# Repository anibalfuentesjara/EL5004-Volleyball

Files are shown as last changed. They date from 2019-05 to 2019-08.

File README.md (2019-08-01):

# EL5004-Volleyball
EL5004 Taller de diseño - Beauchef Proyecta. Proyecto de lanzador de balones de volleyball.

El objetivo del proyecto es realizar un lanzador de balones de volleyball, con el fin de facilitar los entrenamientos del DR de volleyball de la Universidad de Chile y de la rama de volleyball de la universidad. Para esto se trabaja en conjunto con equipos de Ingeniería Eléctrica e Ingeniería Mecánica. El sistema tiene como requisito el poder apuntar el lanzador, ajustar la velocidad de lanzamiento e incorporar un sistema de detección de personas y distintas rutinas de práctica.

El repositorio cuenta con lo siguiente:

- Informe: informe final del ramo.

- Presentación: presentación final del ramo.

- Omni Wrist III: Diseños stl, Solid Edge y Fusion 360 para la base del sistema. Esta base consiste en el sistema Omni Wrist III, que a través de dos motores logra apuntar en los ejes de libertad Pitch y Roll.

- Códigos motor: códigos en arduino para el movimiento de los motores.

- Person Volley: sistema de visión computacional desarrollado en python mediante la librería pytorch. Es el mismo que se adjunta en el github de visión.

- Parabolas: cálculo de parábolas en el lanzamiento del balón.

- Planos eléctricos y lista de materiales: lista de materiales y hardware eléctrico.

- demo: código de arduino que recibe señales de control desde python y mueve servomotores. Es usado en la demo con el modelo 3D impreso.

- comunicacion_wifi: códigos para comunicación wifi entre python y arduino.

- fin de carrera: códigos de fines de carrera.

## Google Drive

Se presentan diversos videos grabados en prácticas del DR.

https://drive.google.com/drive/folders/1kx5sKdnLs_XCrbL7N90hBN0Ewg4CD0pJ

## Sistema de vision

Se presenta el github del sistema de visión y el google drive con los pesos utilizados por el sistema de visión.

https://github.com/Jackerz312/Person_Volley

https://drive.google.com/drive/folders/1hPUGl7ACIlWxsmZmfyyrUkmBOFc591Y6?usp=sharing

## Demo

Se realiza una remo con el modelo del omniwrist impreso en 3D. Para correr la demo el esquemático del circuito es el siguiente:

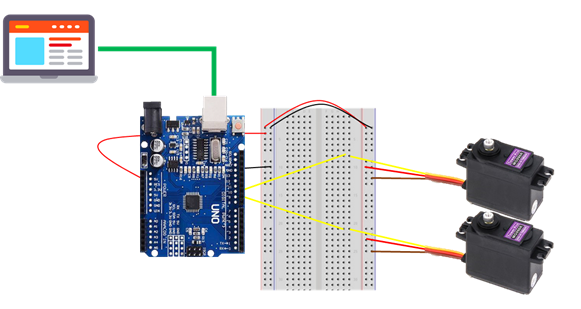
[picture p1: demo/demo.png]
Esquematico demo


Se debe tener cuidado de conectar cada servo en el pin correspondiente. El arduino debe estar conectado con el computador mediante usb. Se debe cargar en arduino el programa demo.ino de la carpeta demo, teniendo cuidado de tener conectado el servo 1 al pin 9 y el servo 2 al pin 10. Luego, existen dos programas de python, en la carpeta person_volley:

- demo_seleccion_libre.py: permite seleccionar un punto en la cancha y apuntar el omni-wrist en esa dirección. En la línea 22 del código se debe tener cuidado de seleccionar el puerto donde está conectado el arduino.

- main_tracking.py: permite seleccionar una persona en el sistema de visión computacional y realizar un tracking de la persona. La persona se selecciona haciendo click sobre la persona en el video. En la línea 64 del código se debe tener cuidado de seleccionar el puerto donde está conectado el arduino. Se puede usar un modelo más rápido cambiando en la línea 61 del código por tini=True.

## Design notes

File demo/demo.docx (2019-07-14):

Arduino_python.ino

Descripción general:

El código permite la recepción de datos desde el puerto serial 9600. Esto se utiliza para recibir los datos de movimiento desde Python para luego realizar el movimiento de motores servo.

Lenguaje: Arduino.

Componentes utilizados:

- 1 Arduino Uno.
- 2 motores servo.
- Fuente de poder para Arduino (se utiliza una de 12 volts).
- Omniwrist.

Conexiones (Esquemático):

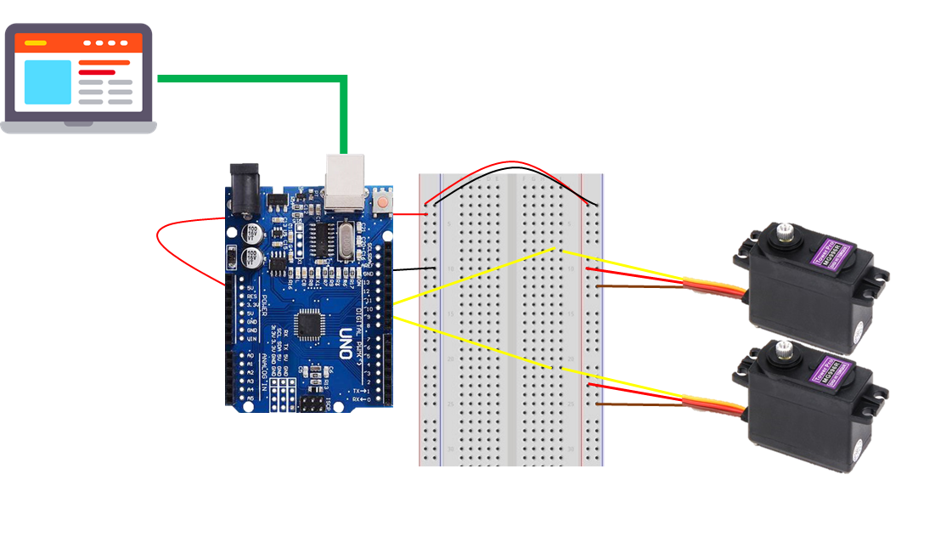
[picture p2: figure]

- Puerto serial en el código debe ser el mismo al que se fije el programa en Python.
- Servos se encuentran conectados al Omniwrist.
- Motores se encuentran conectados a los puertos 9 y 10 en el Arduino.

Descripción del código:

Se inicializan los valores de posición con datos de calibración que permitan que el Omniwrist se ubique en posición vertical.

Se ingresa al loop, que permite la recepción de datos a través del puerto serial. Como lo datos se envían como un String de forma “AnguloServo1#AnguloServo2#VelocidadLanzamiento” se debe pasar los datos a un arreglo de tipo float, para lo que se utiliza la función obtenerDatos.

Posteriormente se les indica esta posición a los motores servo.

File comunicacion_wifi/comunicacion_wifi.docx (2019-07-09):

Comunicación Wifi

La comunicación wifi está encargada de comunicar el computador que procese la parte de visión computacional con el Arduino encargado de mover el lanzador. En particular a través de la comunicación wifi se conecta el computador que procesa el sistema de visión computacional con el Arduino, el cual debe estar conectado al módulo wifi ESP8266 (datasheet https://www.espressif.com/sites/default/files/documentation/0a-esp8266ex_datasheet_en.pdf). Tanto el computador como el Arduino deben estar conectados a la misma red wifi. Los datos a enviar desde el computador al Arduino corresponden a la velocidad de lanzamiento del balón, la elevación de lanzamiento y el ángulo del jugador respecto al lanzador.

En la figura 1 se presenta un esquemático de la conexión del Arduino con el módulo ESP8266.

Figura 1: esquemático de la conexión del Arduino con el módulo wifi ESP8266.

Dentro de los archivos incorporados se encuentra el código SendMessage.py que se ejecuta en Python y envía mediante socket un string al Arduino, el cual será ingresado en la consola donde se ejecute el código Python.

Además, dentro del código está el archivo parsearString.ino que corresponde a un código de Arduino que ejemplifica como parsear datos recibidos como string, los cuales contienen los tres números enviados separados por #, y los guarda como floats en un array; por ejemplo, el código recibe el string 1.32#23.5#44.5 y guarda en el array datos los floats [1.32, 23.5, 44.5]. Se recalca que este código solo ejemplifica el parsear los datos y no utiliza la comunicación wifi.

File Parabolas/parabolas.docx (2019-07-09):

Se presenta el script de Matlab parabolas.m. En este script se simula la trayectoria seguida en un lanzamiento del balón y se proyecta en 2 dimensiones el problema de lanzar el balón de un punto a otro.

El problema se aborda de la siguiente manera:

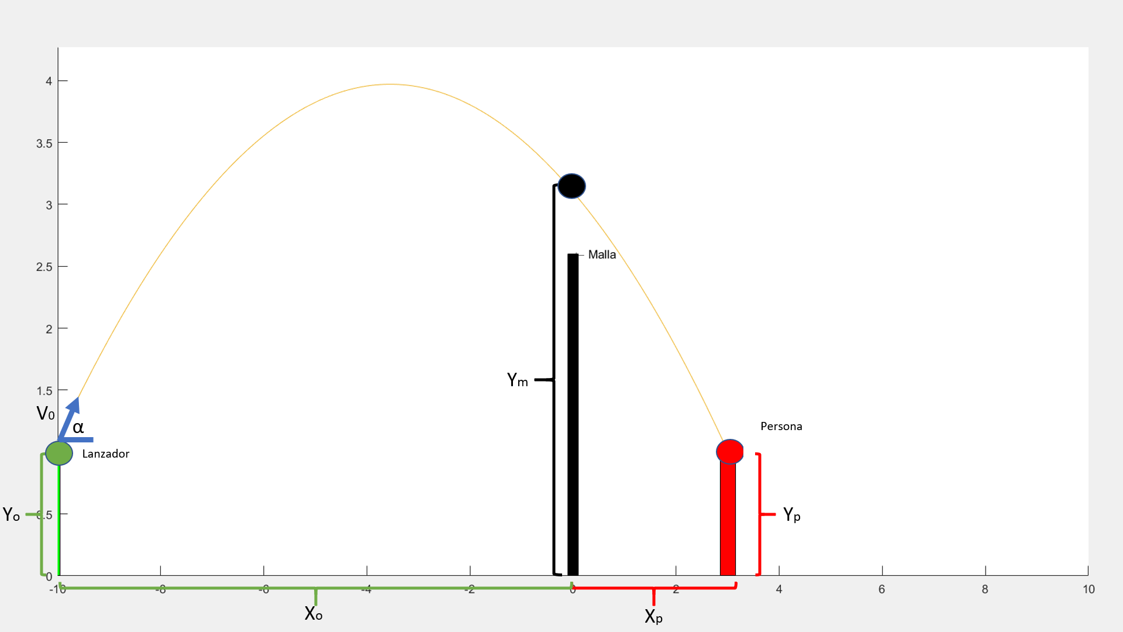
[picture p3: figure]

Dado los puntos (Xo,Yo) representando las coordenadas del lanzador, el punto (0,Ym) representando las coordenadas por la que pasará el balón sobre la malla y las coordenadas (Xp,Yp) representando el punto de recepción del balón; encontrar la velocidad inicial V0 y el ángulo α de elevación con el cual se debe lanzar el balón para que pase por los puntos dados.

Para abordar este problema el primer paso es encontrar la parábola que describe la trayectoria dada; para esto, con los tres puntos disponibles se ajusta una parábola mediante polyfit. Esta parábola está descrita de la forma:

f(x) = A x^2 +Bx+C

Con la ecuación de la parábola posteriormente se encuentra el ángulo de inclinación a través de la pendiente de la parábola evaluada en x = Xo, esto es:

m_(inclinación) =f '(X_o ) = AX_o +B

α=atan(m_(inclinación) )

Una vez encontrado el ángulo se procede a encontrar la velocidad inicial de lanzamiento. Para ello se resuelven las ecuaciones de movimiento del balón considerando los puntos del lanzador y de la persona y descomponiendo la velocidad inicial como:

V_0 =V_0 cos(α)x+V_0 sin(α)y

Las ecuaciones de movimiento se pueden expresar como:

X_p =X_O +V_0 cos(α)T

Y_p =Y_O +V_0 sin(α)T - g T^2

Donde las incógnitas son la velocidad inicial V0 y el tiempo entre el lanzador y la persona igual a T.

Resolviendo este sistema de ecuaciones se llega a:

V_0 =√((0.5g(X_p -X_O )^2)/(cos(α)^2 ((Y_p -Y_O )-tan(α)(X_p -X_O ))))

Y con esto se obtiene el ángulo de inclinación y la velocidad inicial de lanzamiento. Esto es utilizado como base en la parte de visión computacional para calcular los parámetros de lanzamiento del balón.

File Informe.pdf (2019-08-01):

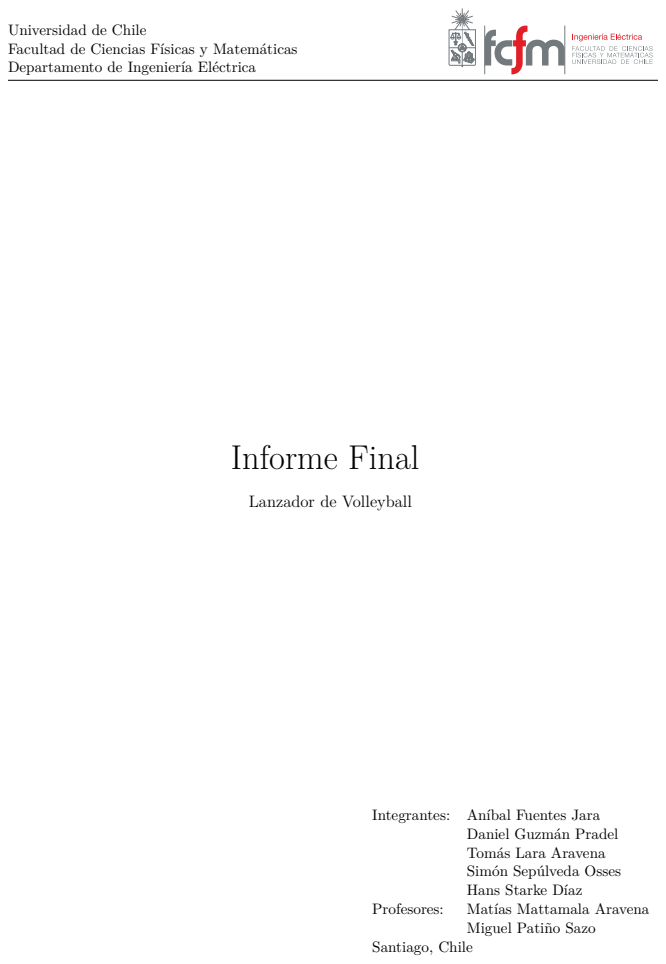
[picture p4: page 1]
Informe Final; Integrantes:; Aníbal Fuentes Jara; Profesores:; Matías Mattamala Aravena; Santiago, Chile

Universidad de Chile
Facultad de Ciencias Físicas y Matemáticas
Departamento de Ingeniería Eléctrica

Lanzador de Volleyball

Daniel Guzmán Pradel
Tomás Lara Aravena
Simón Sepúlveda Osses
Hans Starke Díaz

Miguel Patiño Sazo

Índice de Contenidos | i

# Índice de Contenidos

1. Introducción | 2
2. Solución propuesta | 4
3. Metodología de trabajo | 6
3.1. Equipo de Visión | | 6
| 3.1.1. Detección | | 7
| 3.1.2. Tracking | | 7
| 3.1.3. Transformación de homografía | | 8
3.2. Equipo de Omni-Wrist y Motores | | 8
| 3.2.1. Construcción de Omniwrist | | 9
| 3.2.2. Movimiento con Motores Stepper | | 9
3.2.3. Trabajo con fines de carrera | 10
3.2.4. Cálculo de trayectorias | 11
3.2.5. Ángulos de Giro de motores | 13
3.3. Equipo de Comunicación | 14
3.3.1. ESP8266 | 14
3.3.2. Comunicación con Python | 15
3.3.3. Control de motores | 15
3.3.4. Comunicación Serial | 16
4. Conclusiones y trabajo propuesto | 17

# Lista de Figuras

1 | Esquema de la solución propuesta | | 4
2 | Mecanismo de lanzador | | 5
3 | Esquema sistema de visión computacional | | 6
4 | Diagrama del software de visión computacional | | 7
5 | Puntos seleccionados para realizar la transformación de homografía | | 8
6 | Modelo de omni-wrist III diseñado en fusion 360 e impreso en 3D | | 9
7 | Esquemático de conexión de motores Stepper | 10
8 | Esquemático de conexión de motores Stepper con fines de carrera | 11
9 | Esquema para cálculo de orientación | 12
10 | Esquema para cálculo de elevación y velocidad | 12
11 | Relación entre el ángulo de un motor respecto al reposo, y el ángulo del lanzador. . 13
12 | Módulo ESP8266 | 15
13 | Conexión entre módulo ESP8266 y Arduino | 15
Informe Final | EL5004-3 Taller de Diseño

1

Resumen

En el presente informe se detalla el trabajo realizado durante el curso de taller de diseño Beauchef Proyecta, en el cual se trabajó en el proyecto de lanzador de balones de volleyball.

El proyecto abordado se dividió en tres equipos durante el presente semestre, dos equipos de Ingeniería Mecánica, uno dedicado a la base del lanzador de balones (equipo de omni-wrist) y otro dedicado al lanzador en si (equipo lanzador); el tercer equipo corresponde al equipo eléctrico, cuyo trabajo se detalla en este informe. El trabajo realizado en este equipo esta orientado a la integración del sistema como un todo, centrándose principalmente en tres áreas: el equipo de visión computacional, orientado a la detección de personas dentro de la cancha con el fin de realizar un sistema inteligente que sea capaz de arrojar los balones a los jugadores, el equipo de motores y omni-wrist, encargado del diseño y construcción del omni-wrist, programación de motores, además del cálculo de trayectorias necesarias para disparar el balón en la posición entregada por el equipo de visión, y el equipo de comunicación, encargado de comunicar ambas componentes mediante Wi-Fi.

El resultado del trabajo del semestre corresponde a una serie de módulos que serán útiles para el lanzador final, además de un prototipo a escala, que integra la parte de visión computacional con el omni-wrist, mediante comunicación serial.

Introducción | 2

# 1. Introducción

En el presente informe se muestra el desarrollo de un lanzador de pelotas de Volleyball. Este corresponde a un proyecto multidisciplinario desarrollado en el curso taller de diseño Beauchef Proyecta.
Este proyecto nace en el contexto de que en la universidad existen entrenamientos de volleyball, tanto de la rama de volleyball como de los cursos DR de volleyball, estos entrenamientos se realizan 8 veces a la semana con una duración de aproximadamente una hora y media cada uno, dando un total de 12 horas de juego por semana. Además en este contexto se tiene que existen distintas rutinas de entrenamiento, las cuales son más básicas para el DR, mientras que más exigentes para el DR.
Así, se identifican las siguientes problemáticas:

Acciones de juego disminuyen su velocidad al ser las mismas personas que participan del entrenamiento las que deben realizar los lanzamientos.

Asistencia del entrenador en lanzamientos consecutivos del balón producen desgaste físico en él debido a las largas jornadas de entrenamiento.

Máquinas de lanzamiento de balones mediante rodillos producen daño en estos, lo que implica un alto costo monetario para la institución.

Así, con el contexto y las problemáticas identificadas surge la idea de realizar un lanzador de balones de volleyball que pueda ser utilizado en las prácticas de la universidad.
El proyecto a lo largo del semestre fue abordado por tres equipos, dos de ellos de Ingeniería Mecánica, los cuales se encargaron de diseñar y construir la parte mecánica del lanzador, en particular, un equipo se encargó de la base del lanzador, en el que se desarrolla el mecanismo omni-wrist, un sistema mecánico que ofrece dos grados de libertad para apuntar el lanzador; mientras que el segundo equipo mecánico se encargó de diseñar y construir el brazo del lanzador, que irá montado al omni-wrist y que se encarga de tomar el balón y mediante un mecanismo con resortes similar a una honda disparar el balón.
Por otro lado, el tercer equipo corresponde al equipo de Ingeniería Eléctrica (detallado en este informe), este equipo se encarga de integrar distintas piezas por separado para realizar el sistema como un todo. El trabajo se divide en tres módulos: detección en cancha, movimiento de motores y comunicación entre los dos anteriores.
La detección en cancha se realiza con el uso de dos modelos CNN: YOLOv3 y Tiny YOLOv3, el movimiento orientador del lanzador con Motores Stepper controlado por Arduino y la comunicación entre ambos sistemas con el microcontrolador ESP8266 mediante Wi-Fi.

Del trabajo realizado por el equipo eléctrico se obtienen una serie de resultados:

Diseño de la base del lanzador (omni-wrist) en formato stl.

Prototipo de la base: impresa en 3D, acoplada con servomotores para su movimiento y con un programa para su control.

Sistema de visión computacional: implementado en python y con el uso de herramientas de Deep Learning; nos permite identificar a las personas en la cancha, realizar un tracking de las mismas y seleccionarlas para apuntar hacia ellas.

Introducción | 3

Comunicación Wi-Fi: esquemático y códigos para comunicación Wi-Fi entre el sistema de visión computacional (mediante el lenguaje de programación python) y un arduino, esto con el uso del hardware ESP8266 conectado al arduino.

Códigos para control de motores stepper y calibración mediante fines de carrera.

Cálculos de trayectorias y ángulos para el lanzamiento del balón.

Demo del sistema con prototipo de la base.

Documentación en github.

Este trabajo se encuentra documentado en el github: https://github.com/anibalfuentesjara/EL5004-Volleyball (https://github.com/anibalfuentesjara/EL5004-Volleyball)

Solución propuesta | 4

# 2. Solución propuesta

En base al problema planteado en la sección anterior se plantea como solución un sistema que utilice análisis de imágenes con el fin de a jugadores en la cancha para posteriormente, utilizando un mecanismo de lanzamiento, realizar un disparo de balones hacia el objetivo deseado, indicado a su vez a través de una interfaz amigable al usuario. La solución propuesta se presenta en la figura 1, cuyos diferentes módulos serán detallados a continuación.

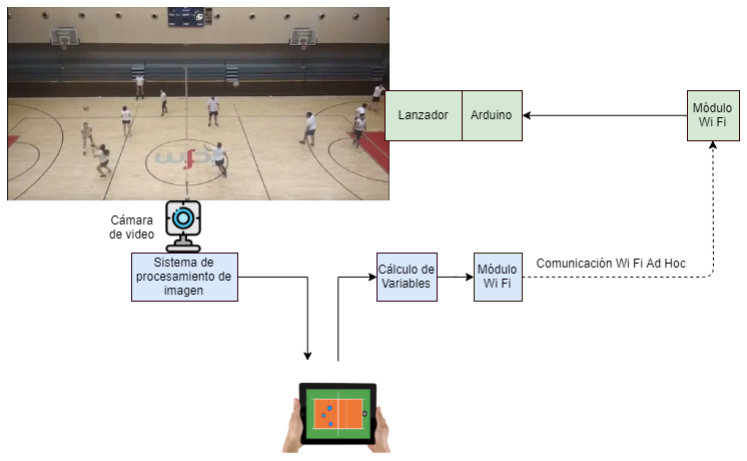
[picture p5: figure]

Figura 1: Esquema de la solución propuesta

Los módulos utilizados de acuerdo a la secuencia en que se utilizan corresponden a los siguientes:

Cámara: Se utiliza una camára de gran ángulo de apertura con el fin de poder capturar la cancha en su totalidad. El sistema plantea el posicionamiento de la cámara en un punto elevado sobre el medio de la cancha, tal como se presenta en la figura 1

Sistema de procesamiento de imagen: El sistema de procesamiento de imagen utiliza las imágenes capturadas por la cámara para detectar a las personas y delimitarlas mediante bounding boxes, adicional a la detección de personas se debe realizar la determinación de sus coordenadas, con el fin de que esta pueda ser utilizada para el cálculo de variables de disparo.

Interfaz con usuario: En la interfaz de usuario, el usuario, en este caso quien guíe el entrenamiento, debe seleccionar el objetivo a enviar el balón.

Cálculo de variables de disparo: En este módulo se debe realizar el cálculo de los ángulos de giro para los motores en el lanzador de modo que el cañón presente la orientación necesaria y el lanzamiento se realice a una velocidad tal que permita alcanzar el objetivo.

Módulo Wi Fi: El módulo Wi Fi debe enviar la información de las variables de disparo al módulo Arduino que se encuentra en el lanzador.

Arduino: La placa Arduino que se encuentra en el lanzador se encarga del manejo de los motores con el fin de realizar el lanzamiento.

Solución propuesta | 5

Lanzador: El lanzador corresponde a la estructura desarrollada por el equipo mecánico que permita el lanzamiento de balones de Voleyball. Imágenes del mecanismo se presentan en las figura 2a y 2b , para el mecanismo Omniwrits que permita apuntar y el lanzador, respectivamente.

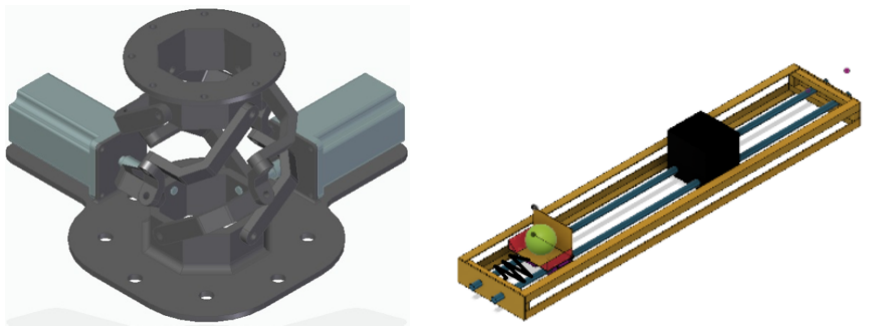
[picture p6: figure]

(a) Omniwrist | (b) Lanzador

Figura 2: Mecanismo de lanzador

Metodología de trabajo | 6

# 3. Metodología de trabajo

Para llevar a cabo el trabajo se dividen las tareas en equipos funcionales, cada uno encargado de un área del proyecto. Estos equipos se conforman como Equipo de omni-wrist y motores, Equipo de visión, y Equipo de comunicaciones. A continuación se presenta la metodología seguida por cada uno de estos equipos presentando los elementos más importantes desarrollados en cada área.

## 3.1. Equipo de Visión

El equipo de visión fue el encargado de entregar al lanzador las coordenadas de los jugadores en la cancha. Esta tarea se divide en tres súbmodulos: detección de personas, tracking y transformación de homografía. Si bien los avances del equipo de visión fueron anexados al github del proyecto estos se encuentran por separado en el github https://github.com/Jackerz312/Person_Volley.
En la Figura 3 se presenta un esquema del sistema de visión computacional, en el se observa la cancha de volleyball, donde sobre ella se ubica una cámara, la cual estará conectada a un computador o un sistema embebido (que será el punto central de procesamiento del lanzador de balones de volleyball), encargado de procesar las imágenes y enviar la información al lanzador

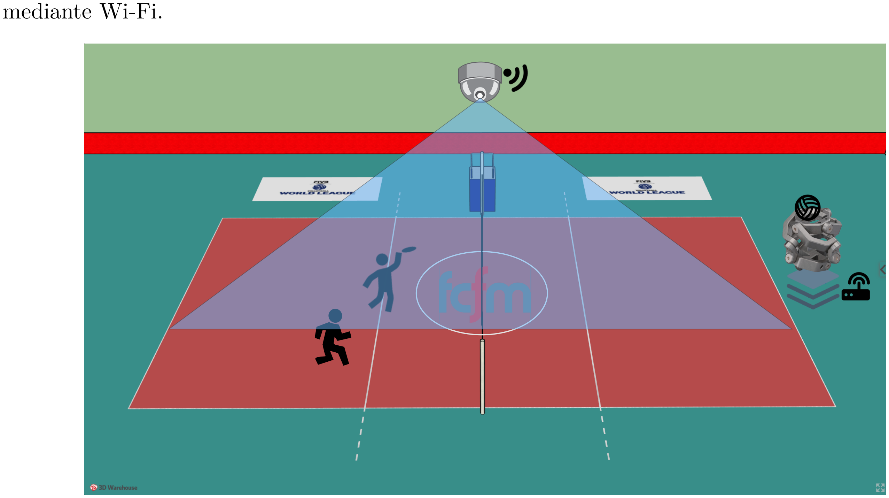
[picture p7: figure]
mediante Wi-Fi.

Figura 3: Esquema sistema de visión computacional.

El software de visión computacional presentará un funcionamiento como el mostrado en la Figura 4, a la izquierda se muestra la imagen capturada por la cámara, sobre esta imagen se realiza la detección de las personas mediante uso de Deep Learning (detección), además, para cada persona detectada se realiza un seguimiento en el tiempo (tracking) para identificar a cada persona de manera separada; finalmente, con las detecciones realizadas se realiza una transformación de homografía que nos permite proyectar a estas personas a sus coordenadas dentro de la cancha, tal como se muestra en la figura 4b, este mapeo nos facilita además el cálculo del lanzamiento del balón. Junto a esto se tiene que, tal como se muestra en la figura, es posible seleccionar a una persona para lanzarle el balón.

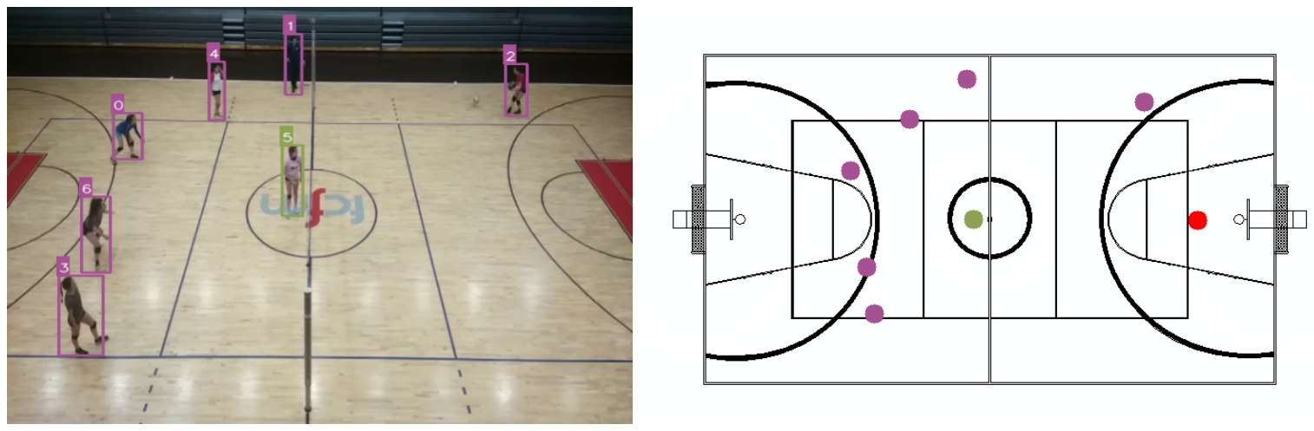
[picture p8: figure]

(a) Detecciones. | (b) Proyección a la cancha.

Figura 4: Diagrama del software de visión computacional.

### 3.1.1. Detección

Uno de los aspectos fundamentales para el proyecto, era la necesidad de contar con la posición de las personas dentro de la cancha. Para esto, se lleva a cabo un análisis de distintas tecnologías que se pueden utilizar, tales como LADAR, RTLS y visión computacional, las cuales se comparan en la Tabla 1, donde se observan las grandes ventajas del sistema de visión por computador frente al resto de opciones, por lo cual es finalmente escogido.

Tabla 1: Ventajas y desventajas de sistemas de detección de personas.

Sistema | Ventajas | Desventajas
RTLS | Alta precisión | - Necesidad de tags
- Poca escalabilidad
LIDAR | - | - Rango acotado
- Desconocimiento de objetos
- Poca escalabilidad
- Baja velocidad de escaneo
Vision Computacional | - Conocimiento de objetos que se observan | - Posibilidad de fallo con baja iluminación.
- Alta escalabilidad
- Capacidad de realizar seguimiento

El modelo de visión computacional escogido corresponde a YOLOv3 [1], debido a alta precisión y velocidad capaz de ser utilizado en tiempo real. Para su uso se entrena en COCO dataset [2] únicamente en datos de personas. Además se entrena una versión liviana llamada Tiny YOLOv3, para su uso en sistemas embebidos. La precisión de los modelos entrenados se muestra en la Tabla 2 utilizando como métrica el mean average precision.

### 3.1.2. Tracking

Para el tracking de personas se utiliza una modificación a implementación de un tracker por centroides [3]. Este tracker consiste en relacionar las detecciones entre cuadros mediante las distan-

Tabla 2: Average precision de modelos entrenados.

Modelo | Mean Average Precision ( %)
YOLOv3 | 73.78
Tiny YOLOv3 | 52.52

cias entre los bounding boxes, donde se asocia un ID al objeto el cual tenga menor distancia entre sus centroides.

### 3.1.3. Transformación de homografía

Para realizar el mapeo de las personas detectadas a la cancha se utiliza el método de transformación de homografía [4]. Este método consiste en encontrar una transformación que sea capaz de relacionar y transformar dos imágenes, a través de ciertos puntos coincidentes. Para ello se consideran los puntos verdes señalados en la figura 5.

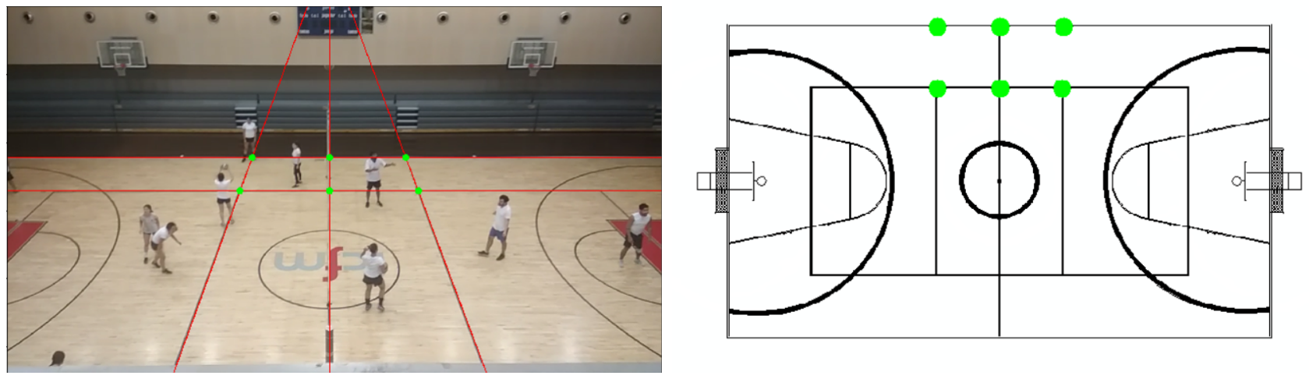
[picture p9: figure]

(a) Imagen capturada | (b) Figura de la cancha

Figura 5: Puntos seleccionados para realizar la transformación de homografía.

Se seleccionan estos puntos debido a que son más fáciles de estimar calculando las intersecciones entre líneas (figura 5(a)), sin embargo, si se tiene la cámara fija es posible seleccionar otros puntos para calcular la transformación de homografía y calcular la transformación solo una vez.
Ya con estos puntos es posible encontrar la transformación mediante la función de openCV find-Homography. Posteriormente, con esta transformación se pueden proyectar puntos de una imagen a otra, tal como se muestra en la figura 4.

## 3.2. Equipo de Omni-Wrist y Motores

El trabajo del equipo de Omni-Wrist y Motores se centró principalmente en el desarrollo de un mecanismo de control del movimiento para el dispositivo “orientador” del lanzador de balones de volleyball, es decir, el Omniwrist III (cuya única referencia es el video en [5]), esto puesto que se tuvo un mayor contacto con este equipo mecánico, además de que para llevar a cabo avances en el módulo lanzador, se debía contar con especificaciones del mecanismo desarrollado por el equipo mecánico correspondiente. El omniwrist III corresponde a un sistema mecánico, que a través de dos motores logra apuntar en los ejes de libertad Pitch y Roll.

Adicionalmente, este equipo desarrolló los cálculos de trayectoria necesarios para determinar los movimientos a realizar por los mecanismos del lanzador. En las siguientes sub secciones se presentan los principales desarrollos realizados por el equipo de motores, los que concluyen con la construcción del prototipo presentado al cuerpo docente.
La documentación de estas secciones se encuentra en el github del proyecto.

### 3.2.1. Construcción de Omniwrist

Con el fin de poder realizar un prototipo que permita probar los principales aspectos del proyecto, como la capacidad de seguimiento de objetivos y la comunicación a través de Wi-Fi, se realiza un modelo de Omniwrist en el programa Fusion360, para posteriormente imprimir este en las impresoras 3D disponibles en Fablab.
El modelo desarrollado en Fusion360 se presenta en la figura 6(a), mientras que el modelo impreso en 3D se presenta en la figura 6(b). Una vez impreso este modelo fue acoplado a una base y se utilizaron dos servomotores para su control, para fines de una demo.

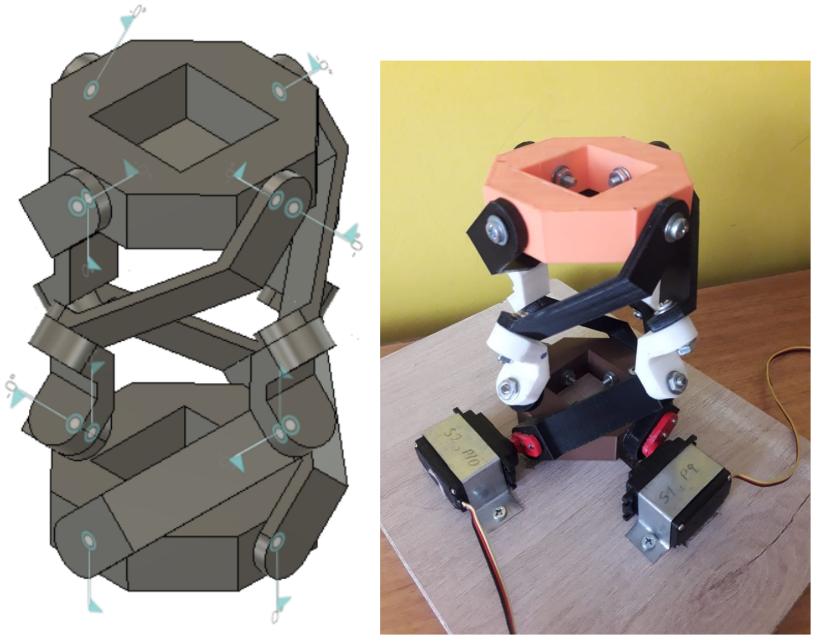
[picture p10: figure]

(a) Modelo diseñado. | (b) Modelo construido.

Figura 6: Modelo de omni-wrist III diseñado en fusion 360 e impreso en 3D.

### 3.2.2. Movimiento con Motores Stepper

El movimiento de los mecanismos de Omniwrist y lanzador fue definido a lo largo del semestre a través del trabajo junto al cuerpo docente y se decidió la utilización de motores stepper, fundamentado principalmente en tres razones. En primer lugar, el torque que presentan estos motores es superior al presentado a otros tipos de motores analizados, lo que se consideró apropiado principalmente para el mecanismo de lanzador, donde este motor, sería forzado a moverse por un resorte estirado una distancia considerable. En segundo lugar, este tipo de motores alcanza una gran precisión en su giro, especialmente al considerar medios pasos en su programación, lo que es útil principalmente en el movimiento que realiza el Omniwrist, destinado a apuntar a jugadores(as) objetivo; Una desventaja de este tipo de motores con respecto a otros corresponde a su falta de retroalimentación, lo que llevaría a complicaciones en caso de que este vea forzado su movimiento, sin embargo, esto se considera improbable debido al torque de los motores y en caso de presentarse sería superado a través del uso de un encoder. Como última razón, la disponibilidad de tres de estos motores en la universidad facilitó el proceso de pruebas en comparación con la necesidad de realizar la cotización y compra de otros motores.
Para el movimiento de los motores stepper se utilizó la librería de Arduino AccelStepper [6]. Esta librería permite mover motores Stepper de distintas configuraciones, permitiendo indicar, por ejemplo, el ángulo objetivo, y la velocidad máxima a alcanzar para llegar a ese ángulo. Estas correspondieron a las variables manipuladas para manejar el movimiento de los motores Stepper. El equemático a implementar para el movimiento de motores stepper utilizando la librería AccelStepper se presenta en la figura 7, donde es posible observar los distintos componentes necesarios para el funcionamiento del motor, correspondientes a la fuente de poder, el controlador (driver) del motor y la placa Arduino que entregue las señales de control al driver.
Utilizando esta configuración se realizan pruebas de movimiento de motores Stepper, utilizando diferentes sentidos de giro, ángulos objetivo y velocidades máximas de movimiento, con el fin de analizar el comportamiento de estos en relación con el torque y precisión de movimiento.

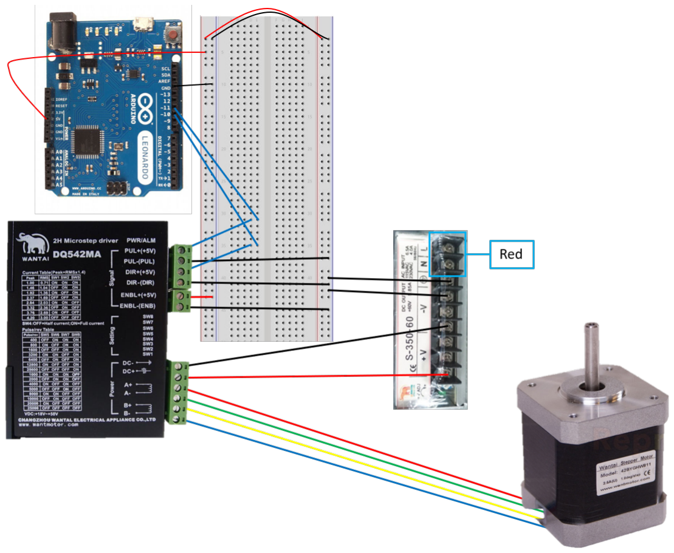
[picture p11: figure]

Figura 7: Esquemático de conexión de motores Stepper.

### 3.2.3. Trabajo con fines de carrera

Como se mencionó en la sección anterior, los motores Stepper a utilizar no poseen realimentación, por esta razón se desarrolla una solución para el movimiento inicial de los motores que incluya el uso de fines de carrera, dispositivos que una vez accionados cambian su estado. En el caso de las pruebas realizadas se utilizan fines de carrera de tipo Makerbot, los cuales al ser conectados a la placa Arduino pasan del estado HIGH a LOW al accionarse, y entregan esta información a la placa.

Se desarrolla un programa en Arduino que permita, a través del uso de interrupciones de tipo FALLING, realizar la calibración de las posiciones iniciales del motor, de esta manera, antes de inicial los movimientos de disparo del motor, se realiza una calibración, correspondiente a conocer la posición inicial de los motores. Para esto, el programa desarrollado realiza un movimiento inicial lento hasta que se accione uno de dos fines de carrera, permitiendo determinar si el motor se encuentra en su posición 0 o 180 grados, para luego conocer las coordenadas bajo las que debe realizar el movimiento. El esquemático de conexiones utilizando dos fines de carrera se presenta en la figura 8.

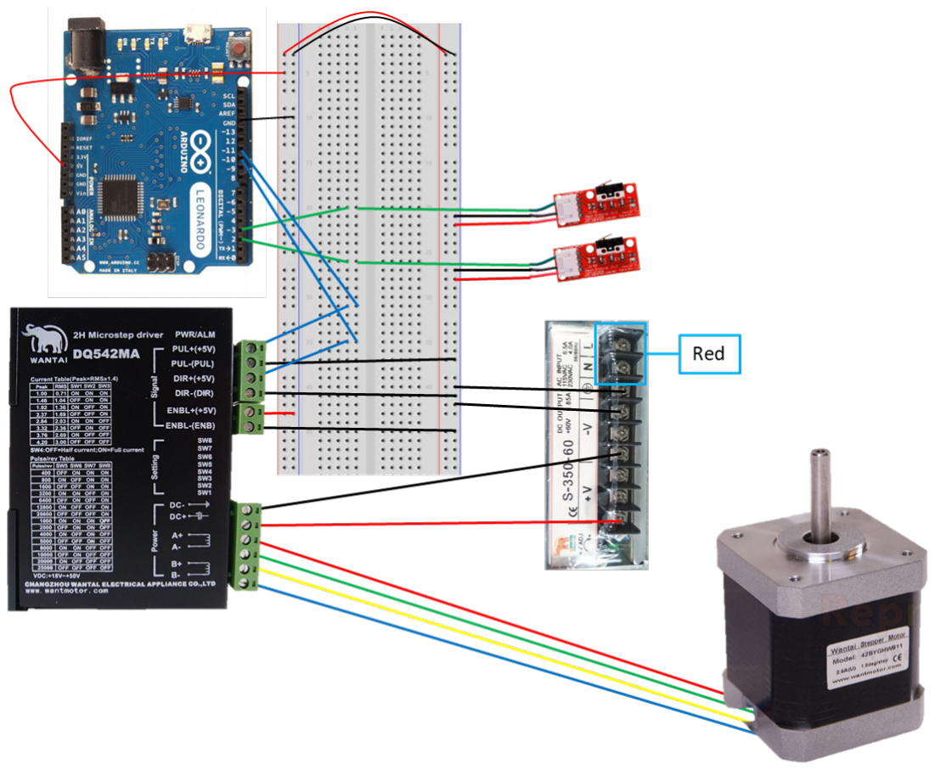
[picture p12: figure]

Figura 8: Esquemático de conexión de motores Stepper con fines de carrera.

### 3.2.4. Cálculo de trayectorias

Para la realización del cálculo de trayectorias se trabaja directamente con el equipo de visión, con el fin de utilizar los puntos (jugadores) determinados mediante mecanismos de visión computacional para calcular las condiciones del disparo del lanzador, correspondiente al posicionamiento del cañon y la velocidad de salida que debiese tener la pelota en su trayectoria hacia el objetivo.
En relación al cálculo de trayectorias, en primer lugar se realiza la determinación de la inclinación que debe tener el cañon al apuntar hacia el objetivo, esto se realiza de acuerdo al modelo plano presentado en la figura 9, donde el punto (x0, y0) representa la posición del lanzador considerada fija, y el punto (xf , yf ) corresponde a la posición del objetivo seleccionado. De acuerdo a este esquema el ángulo a encontrar corresponde a α.

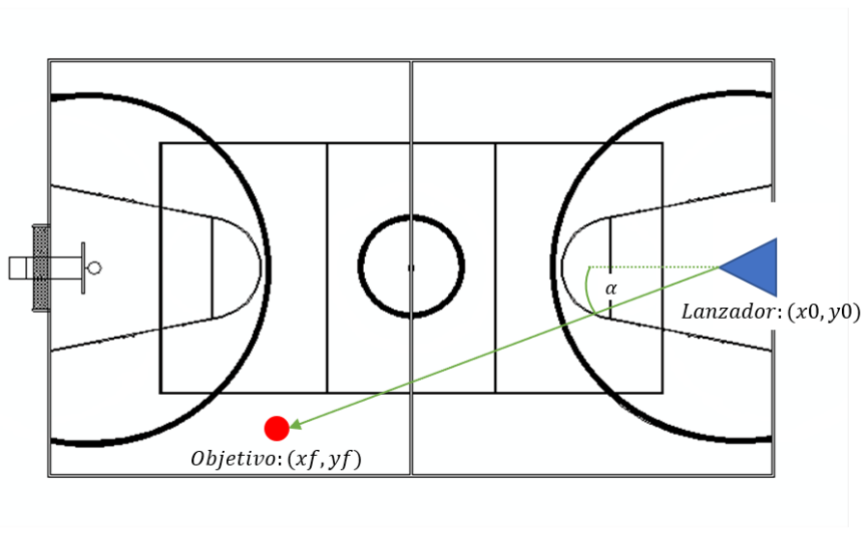
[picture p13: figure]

Figura 9: Esquema para cálculo de orientación.

De esta manera el cálculo de α se realiza mediante la ecuación (1).

α = arctan(

yf − y0
xf − x0
) | (1)

Posterior a esto, es posible reducir el problema de tres a dos dimensiones, donde la distancia que debe horizontal que debe recorrer el balón corresponde a la flecha de color verde en la figura
9. A partir del tratamiento bi dimensional del problema los datos a encontrar corresponden a la elevación del cañon y la velocidad de lanzamiento. Para esto, se define una parábola utilizando tres puntos, en primer lugar, se utiliza como origen el lanzador y como destino la posición del objetivo, como tercer punto se utiliza una posición sobre la malla de mitad de cancha, que posee una altura oficial de aproximadamente 2.6 metros; De esta forma, utilizando la función polyfit de grado dos del módulo numpy de Python es posible obtener los coeficientes de la parábola definida por estos puntos. Utilizando la definición de la parábola es posible obtener la elevación necesaria derivando la ecuación de esta y calculando la tangente, lo que se traduce en evaluar la expresión (2) en el punto donde se encuentra el lanzador donde a y b corresponden al parámetro de segundo y primer grado de la parábola y el ángulo de elevación β se presenta en la figura 10
β = tan(2ax0 + b) | (2)

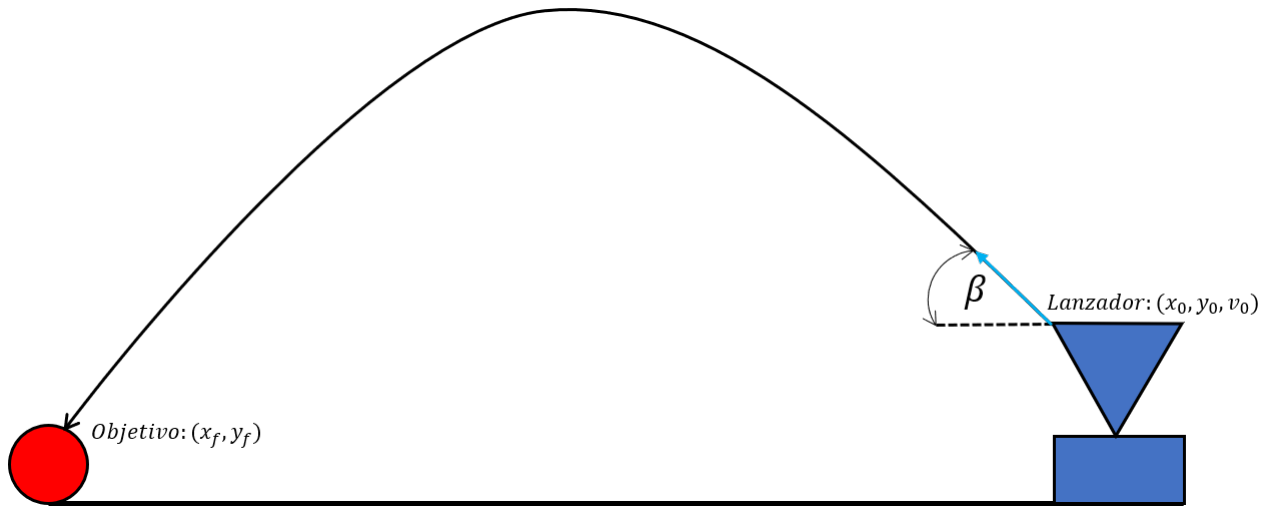
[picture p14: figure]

Figura 10: Esquema para cálculo de elevación y velocidad.

Para el caso de la velocidad es necesario utilizar las ecuaciones cinemáticas del balón en su trayectoria parabólica. A partir de esto es posible encontrar la velocidad que se debe imprimir al balón en la salida para que este llegue al objetivo deseado, la que se presenta en la ecuación (3), donde g corresponde al valor de la aceleración de gravedad, utilizando en este caso un valor de 9.81.

v0 =

s
(0.5 ∗ gxf )

2
cos(β)

2(yf − y0 − tan(β)xf )

(3)

### 3.2.5. Ángulos de Giro de motores

Con el fin de realizar una demostración final del prototipo desarrollado se utiliza el modelo impreso del Omniwrist junto a motores servo; se utiliza este tipo de motores por la facilidad de controlar su posición angular, además de que se contaba con dos de estos a disposición del equipo de trabajo.
Para encontrar el ángulo de los motores es necesario realizar una transformación desde las coordenadas de orientación (α) y elevación (β) presentadas en la sección anterior a ángulos de orientación de ambos motores servo, los cuales se encuentran acoplados al Omniwrist de la manera presentada en la figura 6(b).
Para realizar la transformación se realiza una calibración de los motores, tal que estos posean inicialmente un ángulo de calibración correspondiente a la posición vertical del Omniwrist, posteriormente se debe realizar un transformación desde el vector normal a la superficie del Omniwrist, correspondiente al vector que define la posición del lanzador hasta los ángulos de los motores, considerando que el movimiento en un ángulo arbitrario θ desde el reposo de los motores, influye en la posición del lanzador en un factor de 2θ, tal como se muestra en la figura 11.

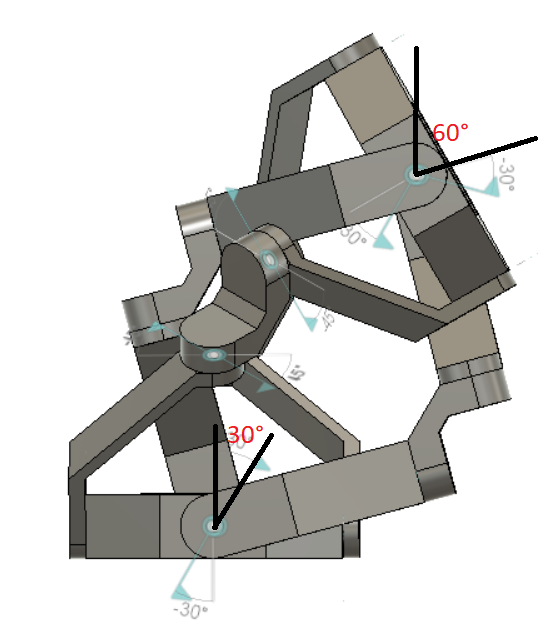
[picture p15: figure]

Figura 11: Relación entre el ángulo de un motor respecto al reposo, y el
ángulo del lanzador.

El ángulo de giro para los motores 1 y 2 indicados en la figura 6(b) (siendo el motor 1 el motor derecho de la figura y el motor 2 el motor izquierdo), se presenta en las ecuaciones (4) y

(5), respectivamente. Donde el ángulo θ corresponde al ángulo en coordenadas esféricas, es decir, θ = 90o − β, de la misma forma que φ = −1 ∗ α

θ1 = −arcsin

sin(θ ∗ π/180) ∗ cos(phi ∗ π/180) 2

∗ 180/π | (4)

θ2 = arcsin

sin(θ ∗ π/180) ∗ sin(phi ∗ π/180) 2

∗ 180/π | (5)

Las ecuaciones anteriores representan los ángulos de movimiento respecto al ángulo de reposo. Cabe destacar que los cálculos anteriormente presentados se realizan en el mismo sistema de visión computacional, utilizando código en Python, de esta manera es posible reducir el costo computacional asociado a la placa de Arduino, pues se envían directamente a este los ángulos de movimiento de los motores servo.

## 3.3. Equipo de Comunicación

El equipo de comunicación es el encargado de obtener las coordenadas en la cancha enviadas por el equipo de visión y comunicarlas al Arduino que controla los motores con el uso del módulo ESP8266. Este tiene una antena Wi-Fi con la cual puede recibir datos y escribirlos en serie a través de sus pines, lo cual se aprovecha para leer con Arduino y controlar los motores como se describe en la sección 3.2.2. Se elige este debido su bajo costo de $3000 1 y compatibilidad con otros microcontroladores.
La comunicación se da entonces entre un servidor local en Python y Arduino, teniendo como intermediario el ESP8266, cual recibe y envía entre ambas a través de la red Wi-Fi a la que se conectan los dispositivos usados.

### 3.3.1. ESP8266

El ESP8266 es un sistema en chip (SoC) desarrollado por la compañía China Espressif [7], cual contiene un microcontrolador y una antena transceptora de Wi-Fi. Este es el intermediario entre el computador que procesa la información visual de la cancha y el controlador de los motores, cual comunica a ambos mediante Wi-Fi.
El módulo se alimenta con 3.3V, cual es de suma importancia respetar puesto que un voltaje superior quema el módulo. Además, requiere corrientes de hasta 300mA, por lo cual es requisito utilizar una fuente de alimentación para él o para el Arduino a cual va conectado. Para realizar las pruebas de este trabajo, se utiliza una fuente de 12VDC y 1A conectada al Arduino. En la Figura 12 se muestra el módulo y su mapeo de pines.

1
https://amgkits.com/home/32-modulo-wifi-esp8266.html?search_query=esp8266&results=10

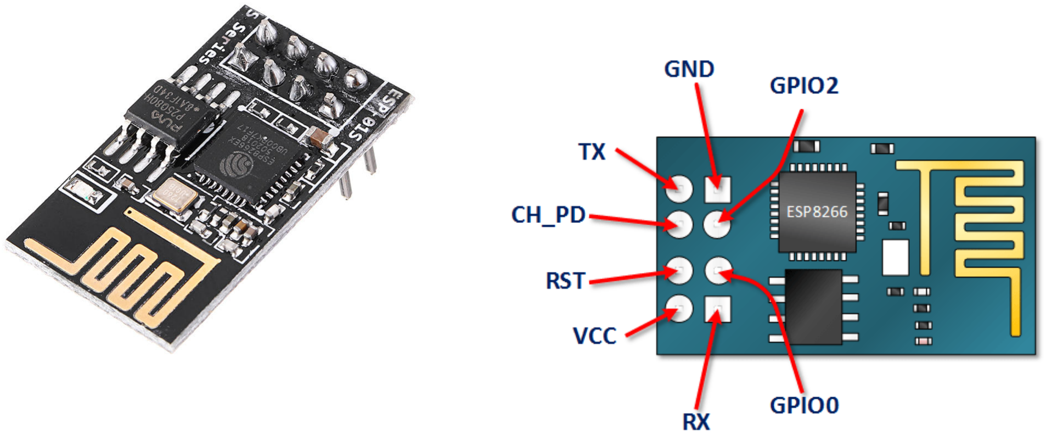
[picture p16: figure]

Figura 12: Módulo ESP8266

### 3.3.2. Comunicación con Python

La comunicación con el sistema de visión se realiza por un servidor local hecho en Python con el uso de la librería socket, cual envía las coordenadas de la cancha a los clientes, en este caso, el módulo ESP8266 cual posteriomente las envía a Arduino. Se realizan la comunicación con Python, puesto que en en este lenguaje es donde se implementa el procesamiento de imágenes.
Las coordenas de orientación y velocidad se reciben como un string separado por # de la forma c1#c2#vel desde Python y se procesan en Arduino para obtener los tres valores como float.

### 3.3.3. Control de motores

Para comunicar el Arduino que controla los motores con el módulo ESP8266 se utilizan las librerías SoftwareSerial, nativa de Arduino y WeeESP8266 disponible en https://github.com/itead/ITEADLIB_Arduino_WeeESP8266. (https://github.com/itead/ITEADLIB_Arduino_WeeESP8266) El esquemático de la conexión se muestra en 13.

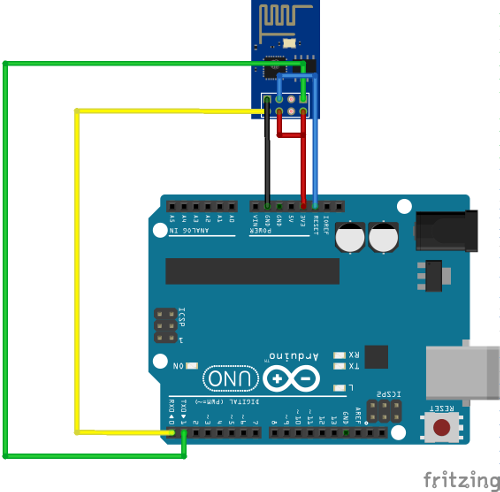
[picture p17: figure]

Figura 13: Conexión entre módulo ESP8266 y Arduino

El objetivo es recibir la información del módulo de visión y entregarlas al script controlador que da la orientación al lanzador.
La librería SoftwareSerial se utiliza para realizar la comunicación por otros pines que son los dedicados para la comunicación de la placa Arduino (0 RX y 1 TX), con el fin de usar estos para el debugging del programa y ver información del estado de la conexión e información recibida, puesto que por defecto estos son los usados para la comunicación con el computador, con lo que si se usan con otro dispositivo, no es posible monitorear la información de salida de la placa. Respecto a esto, se cambia la conexión hecha en los pines 0 y 1 que se ven en la Figura 13 a los pines 2 y 3.
Por su parte, la librería WeeESP ofrece una API de fácil uso, con la cual consultamos la IP de nuestro dispositivo, el estado de la conexión TCP al script de Python y la información recibida para verificar el correcto funcionamiento de las partes.
La comunicación resulta exitosa entre ambas partes, sin embargo presenta una cantidad considerable de pérdida de datos, por lo que muchas veces se entregan coordenadas con dígitos cambiados o sin los separadores, imposibilitando mover correctamente el OmniWrist. Respecto a esto, se requieren métodos de corrección de error si no se desea cambiar la antena WiFi usada.

### 3.3.4. Comunicación Serial

Para confirmar la correcta coordinación entre el sistema de visión y el control de motores, se usa la librería serial de Python, cual permite el envío de datos en serie por puerto USB para recibir las coordenadas sin error. Para usarla, basta conectar el Arduino por USB al computador cual ejecuta el trabajo de visión y especificar el puerto USB al que se conecta. El archivo de ejemplo de uso de este se encuentra en https://github.com/anibalfuentesjara/EL5004-Volleyball/blob/master/Person_Volley/main_tracking.py. (https://github.com/anibalfuentesjara/EL5004-Volleyball/blob/master/Person_Volley/main_tracking.py) Por el lado de Arduino, solo es necesario usar la librería nativa Serial para leer repetidamente. Es requisito que ambos sistemas se comuniquen a la misma tasa de símbolos por segundo (baud rate); en este caso se elige una tasa de 9600 baud.

Conclusiones y trabajo propuesto | 17

# 4. Conclusiones y trabajo propuesto

Durante el curso se pudieron implementar varios aspectos del lanzador de balones de volleyball, los cuales están asociados principalmente a la detección de personas dentro de la cancha y al control de la base del lanzador, para disparar el balón hacia los jugadores. Todo el desarrollo del trabajo quedó documentado en github.
Respecto al desarrollo del curso se recalca que el trabajo con los equipos mecánicos se vio dificultado por la falta de comunicación y contacto con estos equipos, y por la falta de un espacio en común que permita interactuar directamente con ellos.
Con respecto al trabajo propuesto existen diversos puntos a abordar:

Integración con equipo mecánico: se debe integrar el desarrollo realizado con los motores stepper al equipo mecánico, de modo de utilizar los motores stepper en conjunto con los fines de carrera en el modelo del omni-wrist realizado por el equipo mecánico.

Utilización de sistema embebido Nvidia Jetson Nano [8]. Este sistema permite realizar la detección a una tasa de 25 cuadros por segundo en Tiny YOLOv3, además de tener un tamaño compacto ideal para su conexión directa con la cámara para ser instalado en el recinto de manera poco invasiva. Además la adaptación de los códigos actuales es automática debido a que permite utilizar el lenguaje Python junto con las librerías ya utilizadas.

Programa en android para control del lanzador e interfaz de usuario. Esto con la idea de que el lanzador pueda ser controlado de manera remota por el usuario, se pueden interpretar distintas modalidades, entre ellas, lanzamiento a ciertos jugadores seleccionados, lanzamiento a un punto de la cancha o lanzamiento aleatorio.

Control del lanzador y estimación de velocidad de salida. Esto en conjunto con el equipo mecánico del lanzador.

Referencias | 18

# Referencias

[1] J. Redmon and A. Farhadi, “YOLOv3: An incremental improvement,”CoRR, vol. abs/1804.02767, 2018.
[2] Lin TY. et al. (2014) Microsoft COCO: Common Objects in Context. In: Fleet D., Pajdla T., Schiele B., Tuytelaars T. (eds) Computer Vision – ECCV 2014. ECCV 2014. Lecture Notes in Computer Science, vol 8693. Springer, Cham
[3] A. Rosebrock, “Simple object tracking with OpenCV”, Object Tracking, Tutorials, 2018. url: https://www.pyimagesearch.com/2018/07/23/simple-object-tracking-with-opencv/
[4] S. Mallick, “Image Alignment (Feature Based) using OpenCV”, 2018. url: https://www.learnopencv.com/image-alignment-feature-based-using-opencv-c-python/.
[5] https://www.youtube.com/watch?v=BlKM2ayaBGA
[6] https://github.com/waspinator/AccelStepper
[7] Espressif Systems. ESP8266EX Datasheet https://www.espressif.com/sites/default/files/documentation/0a-esp8266ex_datasheet_en.pdf. (https://www.espressif.com/sites/default/files/documentation/0a-esp8266ex_datasheet_en.pdf) Nov. 2018.
[8] Jetson Nano Brings AI Computing to Everyone, url: https://devblogs.nvidia.com/jetson-nano-ai-computing/ (https://devblogs.nvidia.com/jetson-nano-ai-computing/)

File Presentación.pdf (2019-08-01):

# Presentación final:

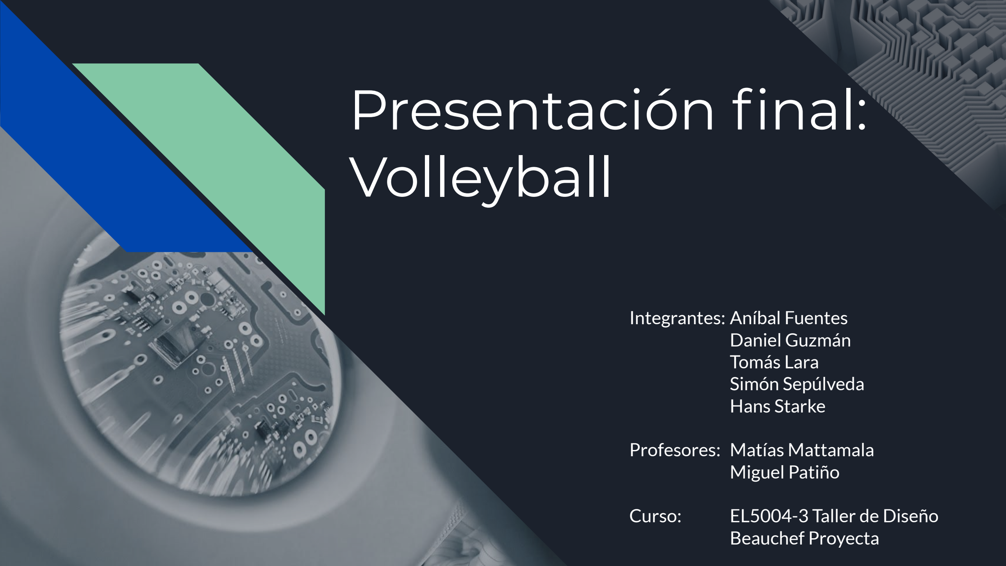
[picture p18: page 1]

# Volleyball

Integrantes: Aníbal Fuentes Daniel Guzmán
Tomás Lara
Simón Sepúlveda
Hans Starke

Profesores: Matías Mattamala Miguel Patiño

Curso: EL5004-3 Taller de Diseño Beauchef Proyecta

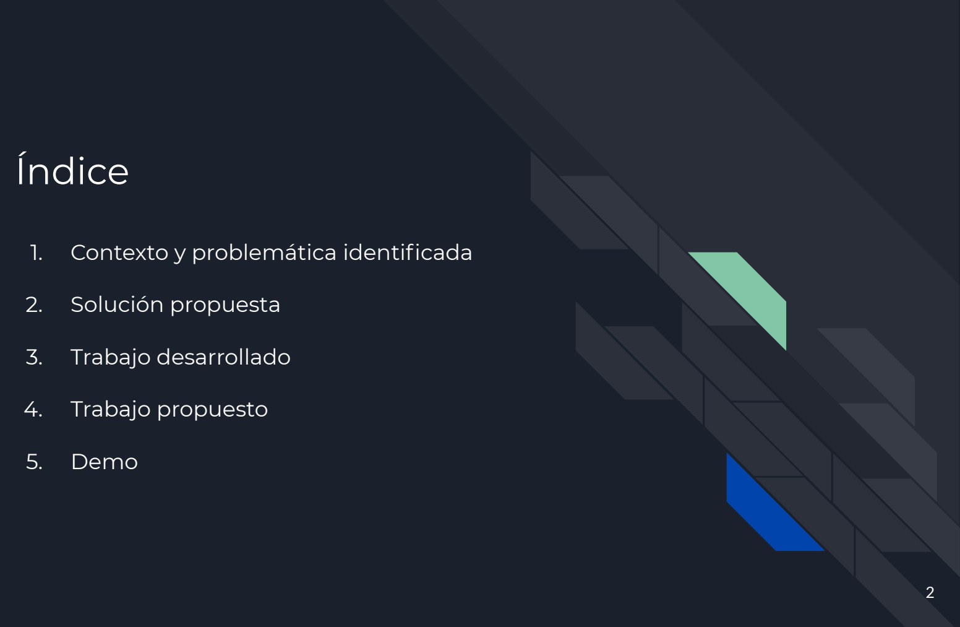
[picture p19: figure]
Índice; 1. Contexto y problemática identificada; 2. Solución propuesta; 3. Trabajo desarrollado; 4. Trabajo propuesto; 5. Demo

# Contexto

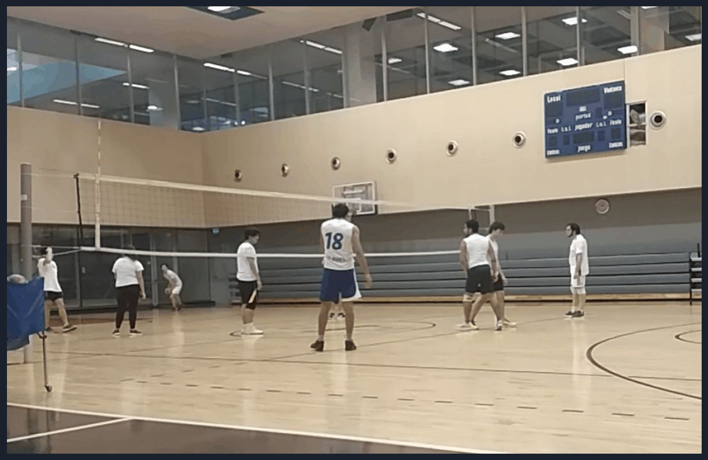
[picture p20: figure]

01 | Entrenamientos de la rama de volleyball de la Universidad, equipo masculino y femenino, dos veces por semana. DR de volleyball, cuatro veces por semana.
02 | Se tienen distintas rutinas de entrenamiento, para el DR más básicas y para la rama más exigente

# Problemática identificada

01 | Acciones de juego disminuyen su velocidad al ser las mismas personas que participan del entrenamiento las que deben realizar los lanzamientos.
02 | Asistencia del entrenador en lanzamientos consecutivos del balón producen desgaste físico en él debido a las largas jornadas de entrenamiento.
03 | Máquinas de lanzamiento de balones mediante rodillos producen daño en estos, lo que implica un alto costo monetario para la institución.

# Solución Propuesta

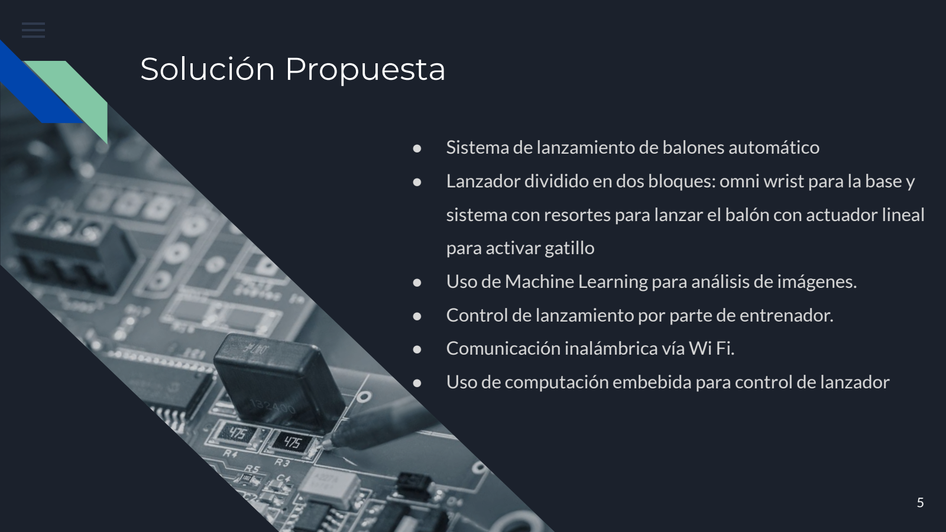
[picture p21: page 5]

- Sistema de lanzamiento de balones automático
- Lanzador dividido en dos bloques: omni wrist para la base y

sistema con resortes para lanzar el balón con actuador lineal

para activar gatillo

- Uso de Machine Learning para análisis de imágenes.
- Control de lanzamiento por parte de entrenador.
- Comunicación inalámbrica vía Wi Fi.
- Uso de computación embebida para control de lanzador

# Solución Propuesta

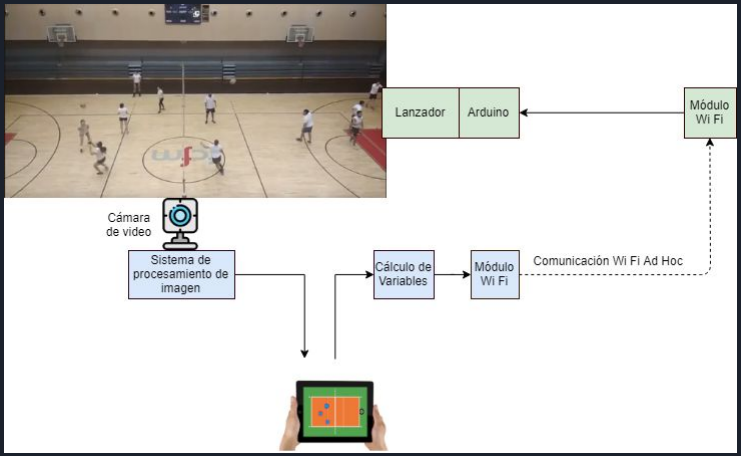
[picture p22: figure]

# Funcionamiento de la solución propuesta

01 | Captura de video utilizando cámara ubicada en posición que permita una visión lateral de la totalidad de la cancha.
02 | Sistema de detección mediante visión computarizada realiza detección de personas, ubicando estas en “bounding boxes”.
03 | Información de video pasa a un módulo WiFi, el que envía un frame de esta información a entrenador para que este pueda decidir dónde realizar el disparo

# Funcionamiento de la solución propuesta

04 | Se calcula velocidad y ángulo de salida, los cuales son enviados a través de un módulo WiFi hasta arduino ubicado en el lanzador,

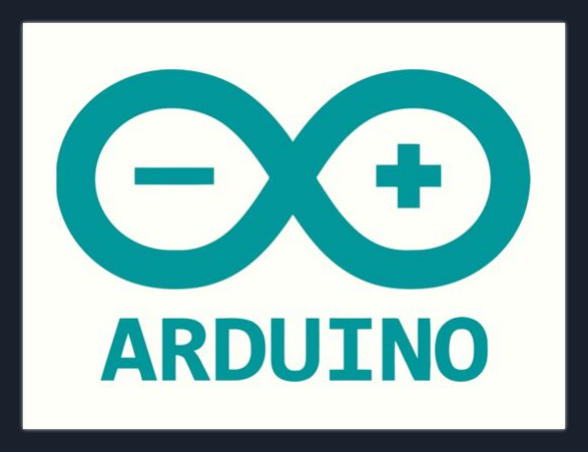
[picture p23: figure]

05 | Arduino recibe las instrucciones del movimiento a realizar y ejecuta el movimiento y carga del lanzador.

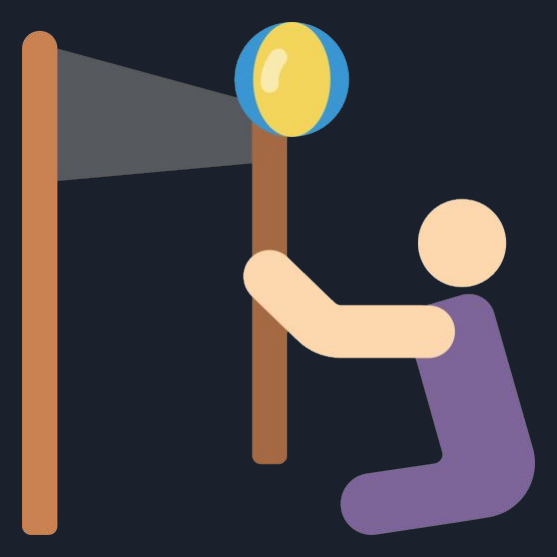
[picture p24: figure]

06 | Lanzamiento!

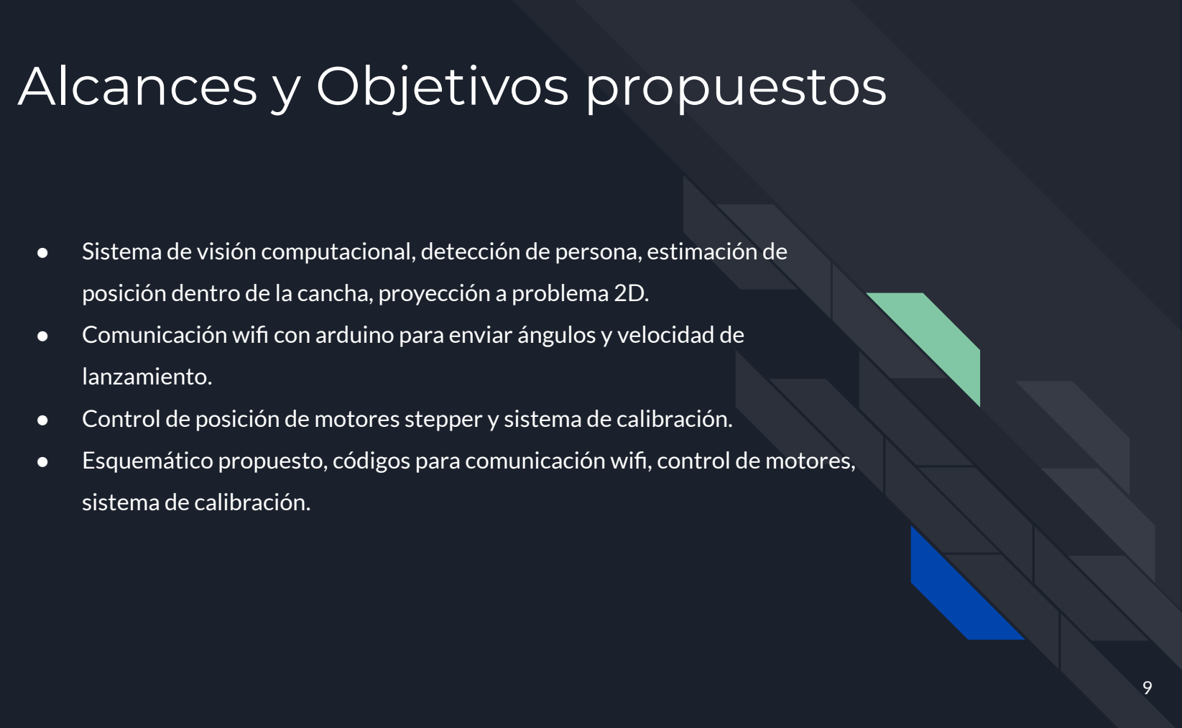
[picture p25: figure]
Alcances y Objetivos propuestos; lanzamiento.; sistema de calibración.

- Sistema de visión computacional, detección de persona, estimación de

posición dentro de la cancha, proyección a problema 2D.

- Comunicación wifi con arduino para enviar ángulos y velocidad de
- Control de posición de motores stepper y sistema de calibración.
- Esquemático propuesto, códigos para comunicación wifi, control de motores,

Trabajo desarrollado; ● Equipo de visión; ● Equipo de omni-wrist y motores; ● Equipo de comunicaciones

# Equipo visión

## - Se propone la instalación del sistema de detección al costado

superior de la cancha.

## - Sistema encargado de la detección de jugadores, el seguimiento de estos y el envío de las variables de importancia al lanzador

mediante Wi-Fi.

## - Se utiliza sistema de detección YOLOv3 junto con seguimiento

mediante centroides.

# Equipo visión


# Equipo visión


# Equipo Visión: Detección y tracking de personas


- Uso de YOLOv3.
- Desarrollo en python con el framework PyTorch.
- Tracking por centroides.
- Proyección a campo 2D.

# Equipo Visión: Proyección


# Equipo de omni wrist y motores


- Trabajo en conjunto a equipo mecánico
- Sistema de movimiento con grados de libertad pitch/roll

# Equipo de omni wrist y motores: construcción omni wrist


Diseño en fusion 360 | Diseño impreso en 3D | 17

# Equipo de omni wrist y motores: Uso de motores stepper


## Motores Stepper:

- Movimiento de Omniwrist.
- Movimiento del mecanismo de lanzamiento.
- Calibración del mecanismo mediante fines

de carrera.

- Desarrollo en arduino mediante librería

AccelStepper

# Equipo de omni wrist y motores: cálculo de trayectorias


- Búsqueda de orientación, elevación y velocidad de salida que permite alcanzar un objetivo.

# Equipo de omni wrist y motores: ángulos de motores


- Búsqueda de ángulos de motores para lograr elevación y orientación calculada anteriormente

# Equipo de comunicación:


- Comunicación wifi mediante módulo ESP8266
- Es el intermediario entre equipo de visión y control de motores
- Envío de posición de motores y velocidad de lanzamiento

# Equipo de comunicación: ESP8266


- Contiene un microcontrolador y antena WIFI
- Funciona a 3.3V máx
- Consume hasta 300mA de corriente, por lo que se DEBE usar con una fuente de alimentación
- Funciona a una tasa de 115200 símbolos por segundo (baud rate)

# Equipo de comunicación: comunicación entre partes


- Comunicación por socket local. Se requiere que los dispositivos estén conectados a la misma red WiFi.
- El script de Python corre un servidor local
- El módulo WIFI actúa como cliente leyendo los datos del servidor
- Luego se escriben de manera Serial hacia Arduino

Trabajo propuesto; por el equipo mecánico.; de usuario.; comunicación Wifi.

- Usar motores stepper y fines de carrera en diseño realizado
- Utilizar sistema embebido para detección (Nvidia Jetson Nano)
- Programa en android para control del lanzador e interfaz final
- Control del lanzador y estimación de velocidad de salida.
- Implementar métodos de reducción de error en la

# Demo


# ¡Gracias por su atención!

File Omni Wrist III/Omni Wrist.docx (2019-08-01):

Omni Wrist

El omni wrist actúa como base del lanzador de balones de volleyball.

Este se basa en el modelo presentado en https://www.youtube.com/watch?v=BlKM2ayaBGA.

Se presentan actualmente dos diseños, en la carpeta diseño eléctricos v1 se encuentra el primer diseño, realizado por el equipo eléctrico. En esta carpeta se tienen 4 archivos, el archivo omni wrist movimiento v10.f3d es un archivo que presenta el diseño completo realizado, y se abre con el programa fusión 360. Además, se presentan tres archivos stl que corresponden al octágono, al brazo largo y al brazo corto, estos archivos se abren con cualquier programa de modelado 3d. En la figura 1 se presenta el diseño del omni wrist realizado por el equipo eléctricos.


Figura 1: Diseño del omni wrist realizado por el equipo eléctrico.

Por otro lado, se tiene el segundo diseño realizado, el cual fue realizado posteriormente por el equipo mecánico. En la carpeta diseño mecánicos v1 se presenta este diseño. Además, hay dos subcarpetas, en la primera se encuentra el diseño realizado en solid Edge, mientras que en la segunda se presenta el diseño en formato stl con cada una de sus partes por separadas y además todas juntas. Finalmente, en la figura 2 se presenta el diseño del omni wrist realizado por este equipo.


Figura 2: Diseño del omni wrist realizado por el equipo mecánico.

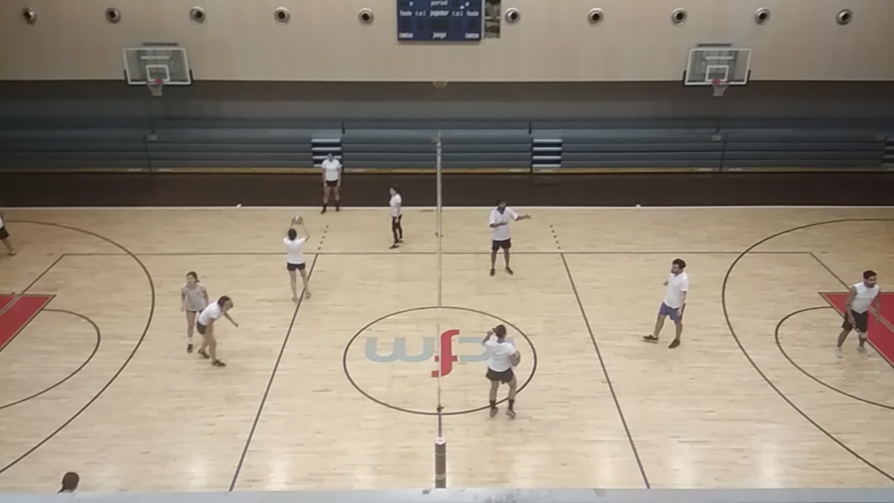
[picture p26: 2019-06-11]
Person_Volley/imagenes_videos/imagen_cancha.png

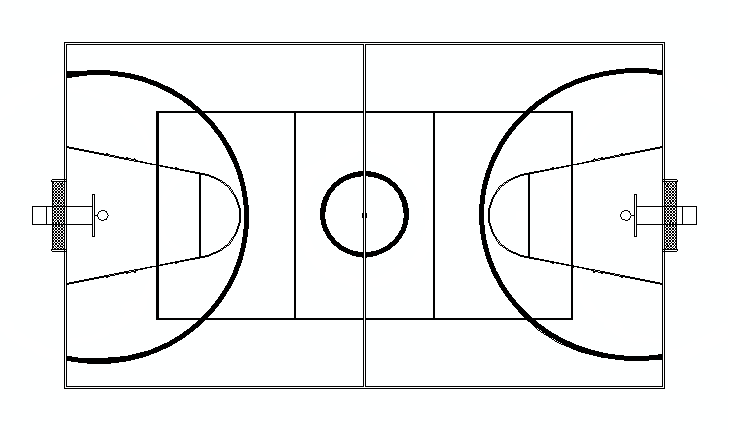
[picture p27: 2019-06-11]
Person_Volley/imagenes_videos/dibujo_cancha.png

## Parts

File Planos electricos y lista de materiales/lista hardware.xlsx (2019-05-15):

Omni wrist y lanzador
Item | Modelo | Descripción | Cantidad | Estado | Más
Motor Stepper | 85BYGH450D-008 | Motores stepper para omni wrist y lanzador | 3 | Listo
Driver Motor | DQ860MA | Driver para motores stepper | 3 | Listo
Fuente de poder |  | Fuente de poder para drivers de motores stepper | 3 | Listo
Arduino | Leonardo | Arduino para control del sistema | 1 | Listo
Fines de carrera |  | Microswitch de palanca o switch de final de carrera | 3 |  | https://www.gobantes.cl/control-y-potencia/interruptores-fin-de-carrera-microswitsh-ekoline?product_id=14544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
Sensor óptico de barrera |  | Sensor para detectar velocidad de salida del balón | 2 |  | https://www.ingmecafenix.com/automatizacion/sensor-optico/
Actuador lineal |  | Actuador lineal para gatillar sistema de disparo | 1
Módulo wifi |  | Módulo wifi para comunicación de arduino y sistema de visión | 1
Sistema de visión
Item | Modelo | Descripción | Cantidad | Estado | Más

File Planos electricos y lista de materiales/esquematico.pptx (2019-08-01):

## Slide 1

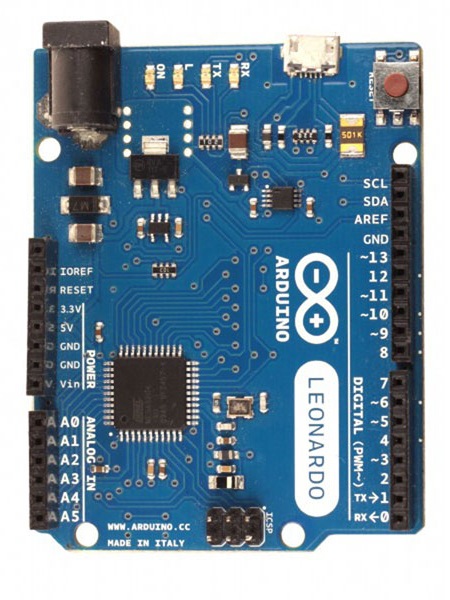
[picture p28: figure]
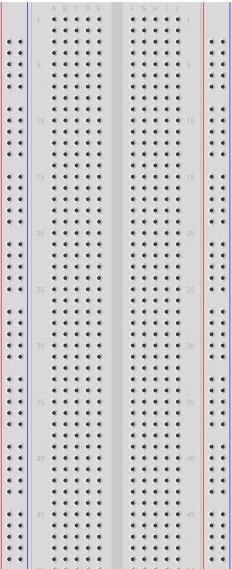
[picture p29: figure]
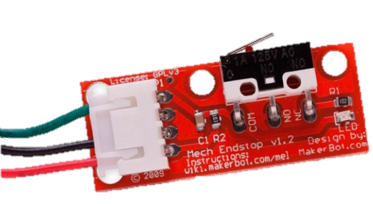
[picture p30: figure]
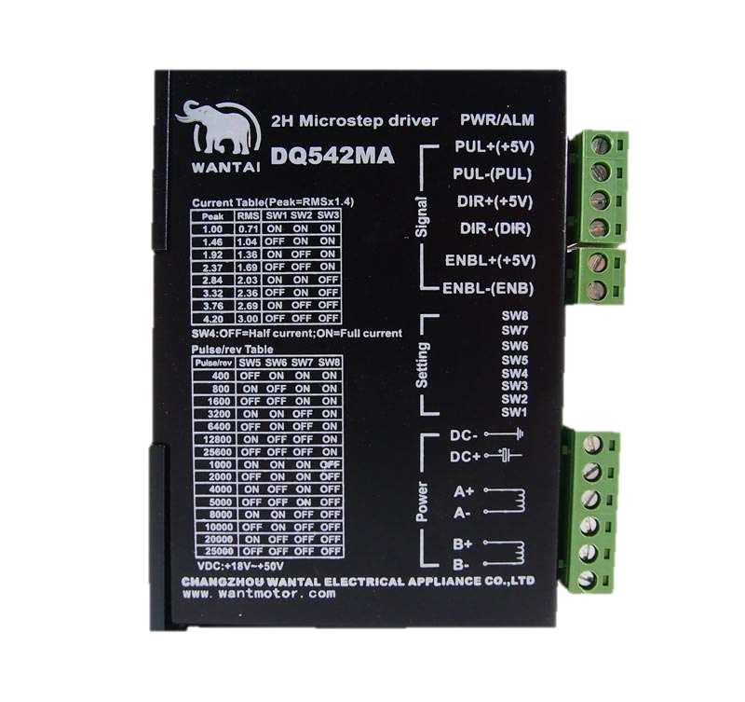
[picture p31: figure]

Red

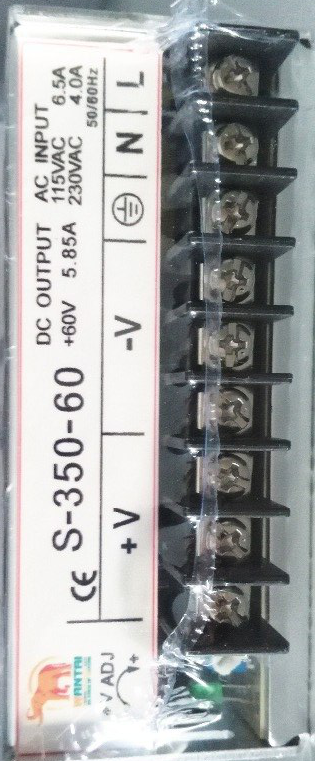
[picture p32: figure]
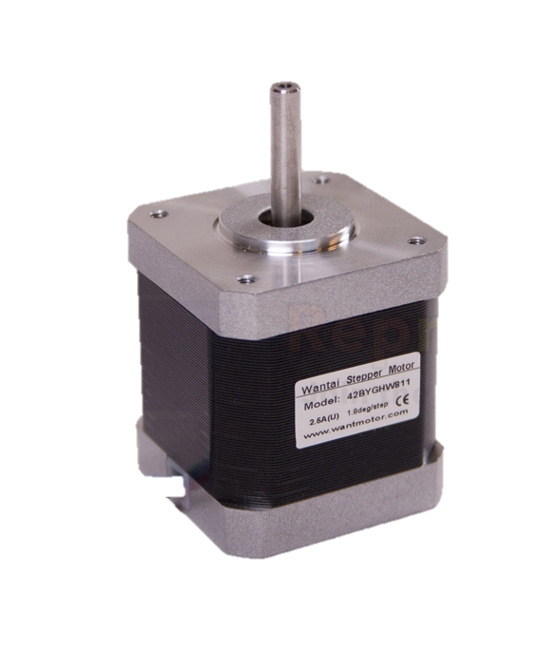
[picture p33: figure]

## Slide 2

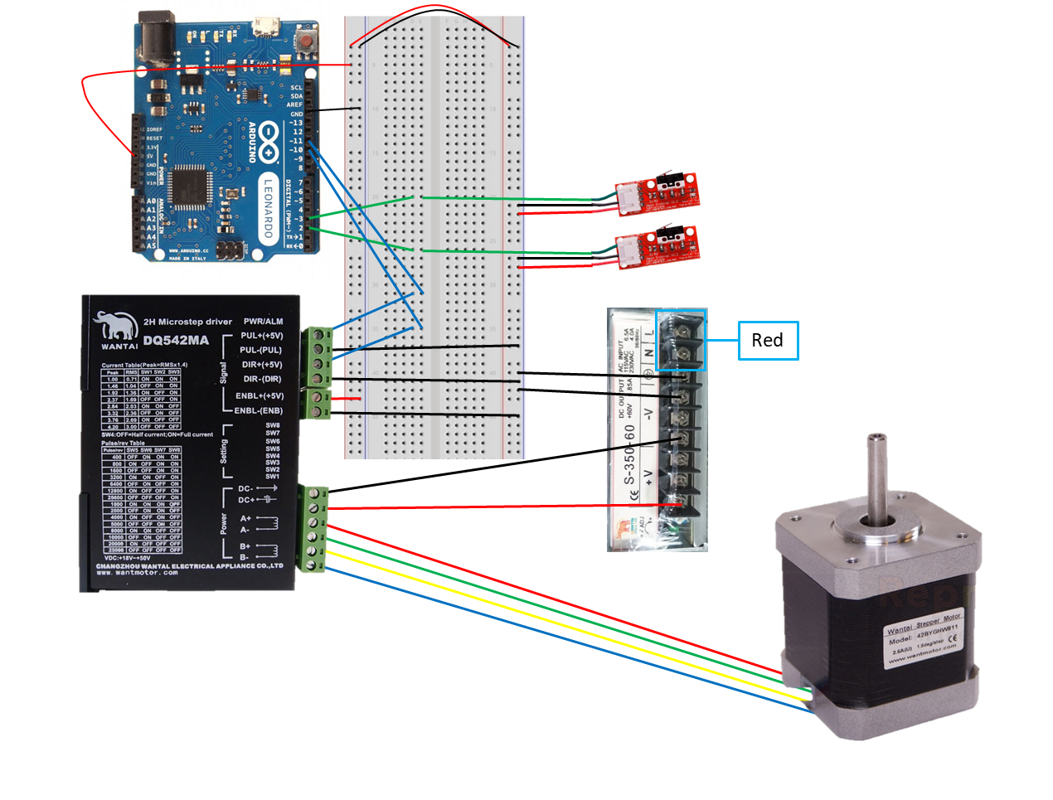
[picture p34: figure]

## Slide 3

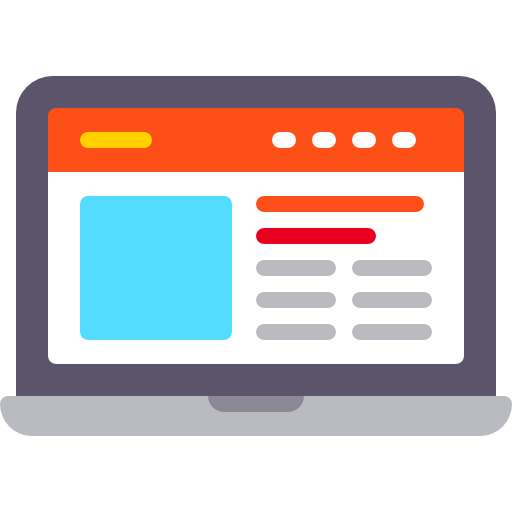
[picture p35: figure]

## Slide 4

Red

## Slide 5


α

Lanzador:(x0,y0)

Objetivo:(xf,yf)

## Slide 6

β

Lanzador:(x_0 ,y_0 ,v_0 )

Objetivo:(x_f ,y_f )

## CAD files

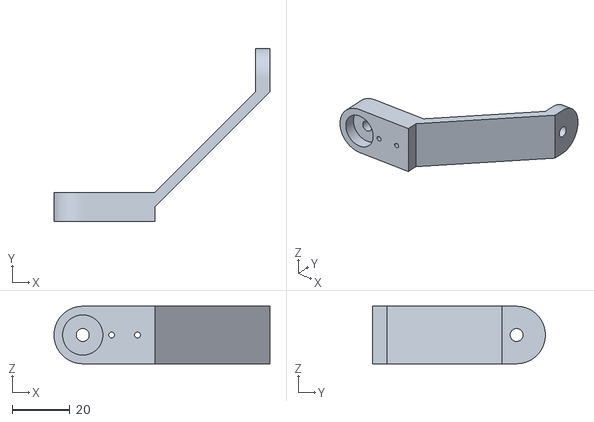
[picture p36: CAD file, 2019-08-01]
Omni Wrist III/diseño electricos v1/brazo largo servo.stl
75.0 x 60.0 x 20.0

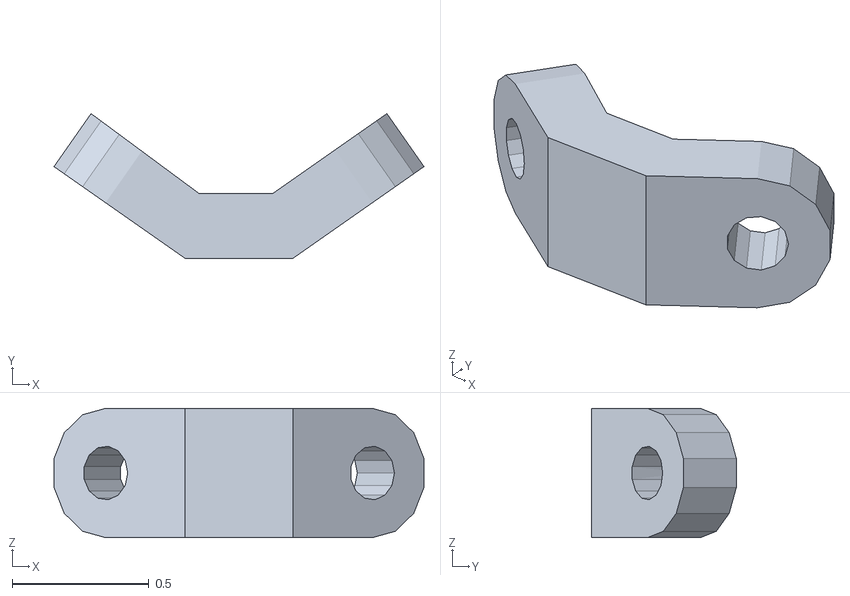
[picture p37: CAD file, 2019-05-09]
Omni Wrist III/diseño mecanicos v1/Piezas y ensamble en formato STL/brazopeqomni.stl
1.35 x 0.529 x 0.472

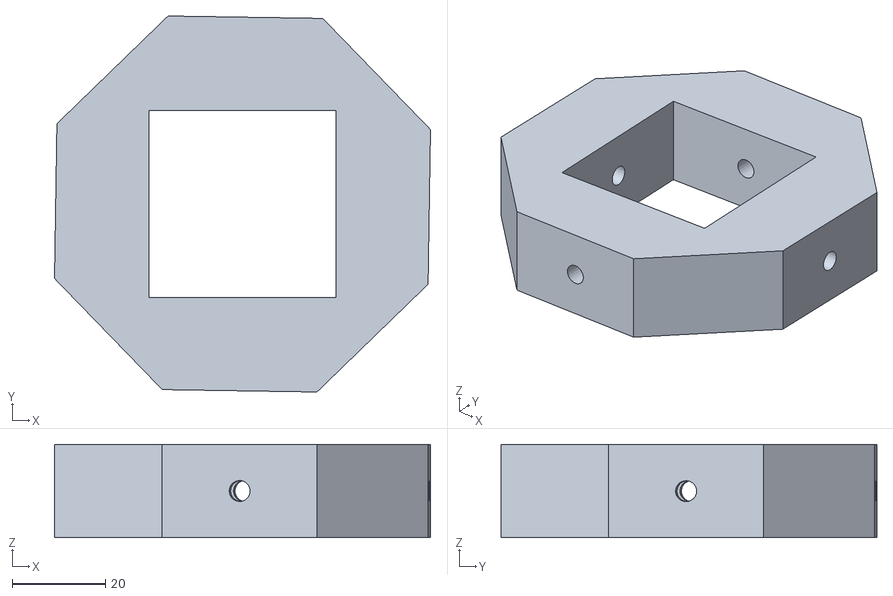
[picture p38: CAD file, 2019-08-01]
Omni Wrist III/diseño electricos v1/octagono.stl
80.5 x 80.5 x 20.0

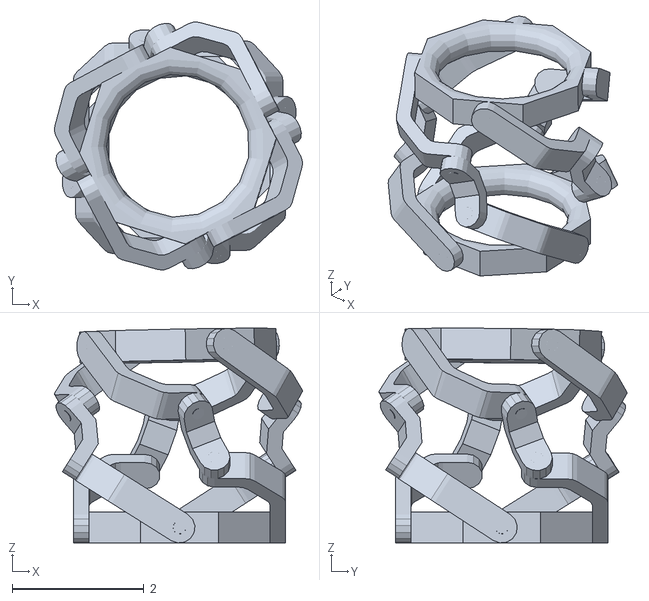
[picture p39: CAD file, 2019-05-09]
Omni Wrist III/diseño mecanicos v1/Piezas y ensamble en formato STL/Omni Wrist.stl
3.77 x 3.77 x 3.27

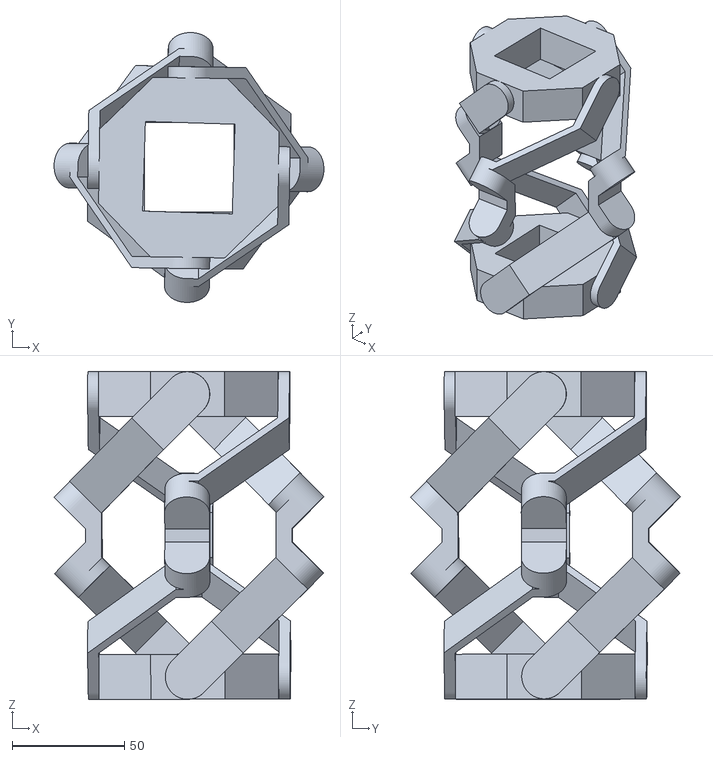
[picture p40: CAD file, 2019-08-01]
Omni Wrist III/diseño electricos v1/omni wrist.stl
120.3 x 120.3 x 146.3

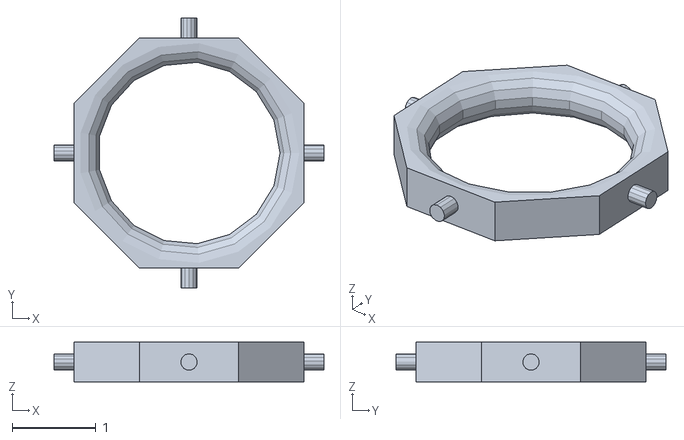
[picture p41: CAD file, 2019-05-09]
Omni Wrist III/diseño mecanicos v1/Piezas y ensamble en formato STL/baseomni.stl
3.23 x 3.23 x 0.472

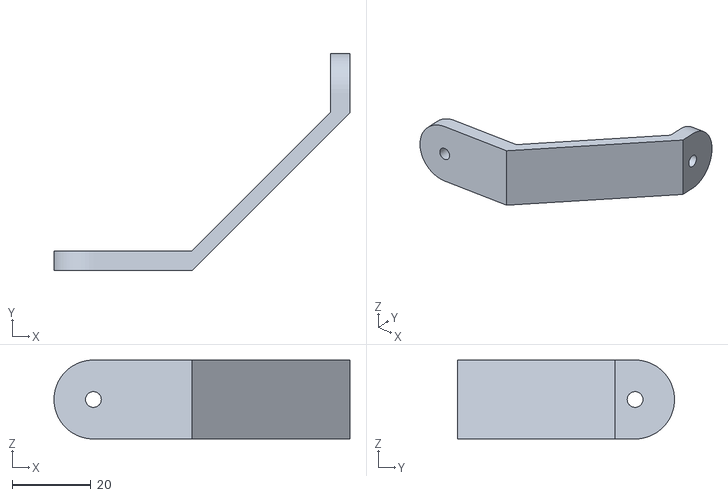
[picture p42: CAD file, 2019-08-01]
Omni Wrist III/diseño electricos v1/brazo largo.stl
75.0 x 55.0 x 20.0

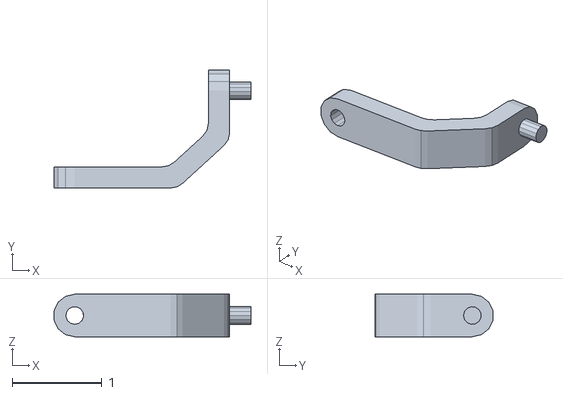
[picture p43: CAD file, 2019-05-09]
Omni Wrist III/diseño mecanicos v1/Piezas y ensamble en formato STL/brazomni.stl
2.19 x 1.31 x 0.472

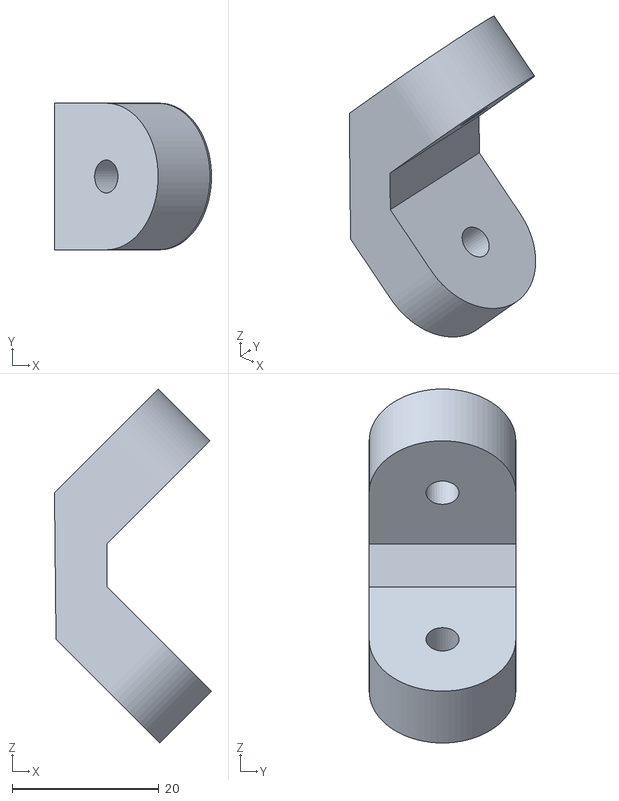
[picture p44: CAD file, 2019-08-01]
Omni Wrist III/diseño electricos v1/brazo corto.stl
21.4 x 20.0 x 48.3

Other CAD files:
Omni Wrist III/diseño electricos v1/omni wrist movimiento v10.f3d
Omni Wrist III/diseño electricos v1/omni wrist.f3z

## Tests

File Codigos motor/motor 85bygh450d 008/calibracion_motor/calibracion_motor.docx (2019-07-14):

Calibracion_motor.ino

Descripción general: El código tiene como función implementar la calibración de los motores stepper utilizando fines de carrera. Se realiza la calibración de los ángulos 0 y 180. La calibración es necesaria pues los motores no poseen una retro alimentación que les permita conocer su posición efectiva.

Lenguaje: Arduino.

Componentes utilizados:

- 1 Arduino Leonardo.
- 2 Fines de Carrera (Endstop) tipo Makerbot.
- 1 motor stepper. Marca: Wantai. Modelo: 85DYQH450D-008
- Driver correspondiente al motor.
- Fuente de poder.

Conexiones (Esquemático):


- Conexiones al controlador (driver): Desde el motor conectar el cable rojo a terminal A+, verde a terminal A-, amarillo a terminal B+ y azul a B-.
- El número de pulsos por revolución indicado en el driver deber ser el mismo que se indica en el código de Arduino.
- Pines utilizados para las interrupciones varían de acuerdo a la placa Arduino utilizada.

Descripción del código:

Se definen los pines de interrupción, en el caso del código incluido se utilizan los pines 2 y 3, estos pines pueden variar dependiendo de la placa Arduino que sea utilizada, en este caso se utilizó un Arduino Leonardo.

Se fijan los pulsos por revolución los cuales deben coincidir con los indicados en el driver.

El código se encuentra escrito de modo de que se realice una calibración inicial del motor, para esto se fija la variable activar_calibracion como true.

Se definen las dos interrupciones en el setup, cada una de las interrupciones llama a un método distinto siendo en el primer caso el método que define la posición del motor como 0° y la segunda como 180°. Cabe notar que estos ángulos deben tener asidero en la realidad física del prototipo puesto que estos deben ser ubicados en los ángulos en los que se pretenda realizar la calibración. Cabe notar además que las interrupciones corresponden al tipo FALLING, esto debido a que los fines de carrera presentan un nivel alto (HIGH) al no ser accionados y bajo al encontrarse presionados (LOW).

Finalmente se realiza un movimiento lento del motor hasta que este accione alguno de los fines de carrera y fije su posición instantánea.

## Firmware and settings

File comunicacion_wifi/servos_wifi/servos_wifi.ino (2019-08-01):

#include <Servo.h>
#include "ESP8266.h"
#include <SoftwareSerial.h>

//Nombre de la red wifi a la que todos los dispositivos se conectan
#define SSID        "Danig"

//Password de la red wifi
#define PASSWORD    "volleyball"

//Nombre del host. Se obtiene del sv en Python.
//Usando la libreria socket, se llama a socket.gethostname()
#define HOST_NAME "DESKTOP-NS8ENN1"

//Puerto. Dejarlo asi
#define HOST_PORT (88)



SoftwareSerial ESP(3, 2); // RX, TX 
ESP8266 wifi(ESP,115200);

Servo myservo1;
Servo myservo2;
float datos[3] = {92.0, 83.0, 10.0};
int pos = 0;
 
void setup() 
{
   Serial.begin(115200);
   myservo1.attach(9);  // attaches the servo on pin 9 to the servo object
   myservo2.attach(10);  // attaches the servo on pin 9 to the servo object
   Serial.print("setup begin\r\n");
   delay(3000);
  
   if (wifi.joinAP(SSID, PASSWORD)) {
         Serial.print("Join AP success\r\n");
   }  
   else {
         Serial.print("Join AP failure\r\n");
   }
 
   Serial.print("setup end\r\n");
 
 
}
 
void loop()
{
  //Lectura de los datos
  delay(1000);

  //Conexion con la API
  uint8_t buffer[256] = {0};  

  if (wifi.createTCP(HOST_NAME, HOST_PORT)){
    //Serial.print("create tcp ok\r\n");

    
    uint32_t len = wifi.recv(buffer, sizeof(buffer), 5000);
    char coordenadas[len+1] = "";
    if (len >= 0) {
        for(uint32_t i = 0; i < len; i++) {
            coordenadas[i] = (char)buffer[i];
        }
        coordenadas[len]='\0';
        Serial.println(coordenadas);
        obtenerDatos(coordenadas);
        myservo1.write(datos[0]);
        myservo2.write(datos[1]);
     
    }
    
  }
  else {
    Serial.print("create tcp err\r\n");
  }   
  
}
 
 

void obtenerDatos(String textoRecibido){
  int contador = 0;
  int inicio = 0;
  for (int i = 0; i < textoRecibido.length(); i++)
  {
    if (textoRecibido.substring(i, i+1) == "#")
    {
      if (contador==1){
        datos[contador] = textoRecibido.substring(inicio,i).toFloat();
        datos[contador + 1] = textoRecibido.substring(i+1).toFloat();
      }
      else{
        datos[contador] = textoRecibido.substring(inicio,i).toFloat();
      }
      contador = contador + 1;
      inicio = inicio + i + 1;
    } 
  }  
}

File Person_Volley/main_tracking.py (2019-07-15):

import random
import os.path
import urllib.request
import torch
import numpy as np
import matplotlib.pyplot as plt
import yolov3 as yolo
import cv2
from courtTransformation import getCourtTransformMatrix,transform_point
from calculosLanzamiento import pass_function, calculo_orientacion_elevacion_velocidad, angulos_motores
import time
import serial
from centroidtracker import CentroidTracker

#from sort import Sort

Persons_pos=[]
Person_des=[]
inputw=608
inputh=544
outputw=720
outputh=480
FONT = cv2.FONT_HERSHEY_SIMPLEX

def select(event, x, y, flags, param):
    global Persons_pos,Person_des   
    #Transformacion de tamaños
    x*=inputw/outputw
    y*=inputh/outputh
    if event == cv2.EVENT_LBUTTONUP:
        for Person in Persons_pos:
            if Person[1]<=x and Person[3]>=x and Person[2]<=y and Person[4]>=y:
                Person_des=[Person[0]]


def load_model(tiny = False):

    if tiny:
        weights_path = 'data/yolov3-tiny_final.weights'
        config_path = 'data/yolov3-tiny.cfg'
    else:
        weights_path = 'data/yolov3-spp_final.weights'
        config_path = 'data/yolov3-spp.cfg'
    #labels_path = 'data/obj.names'

    # Create YOLO detector
    model = yolo.Detector(config_path=config_path,
                          weights_path=weights_path,
                          input_size=(544, 608),
                          conf_thresh=0.25,
                          nms_thresh=0.4)

    if torch.cuda.is_available():
        model.cuda()  
    
    return model


def main():
                        
    model = load_model(tiny=False)
    arduino_on = True
    try:
    	arduino = serial.Serial("COM11", 9600)
    	print("Comunicacion con el arduino exitosa")
    except:
    	arduino_on = False
    	print("No se puede comunicar con arduino")

    n_frames_comunicacion=12
    iterador_comunicacion=0

    posicion_omni = (582, 216)

    # Dibujo   
    img_dibujo = cv2.imread("imagenes_videos/dibujo_cancha.png",1)
    img_dibujo_copy = img_dibujo.copy()
    shape_dibujo = img_dibujo.shape

    #Variables para enviar a arduino
    orientacion=0
    elevacion=0 
    velocidad=0
   

    save_video = False    
    if save_video:
        fourcc = cv2.VideoWriter_fourcc(*'MP4V')
        out = cv2.VideoWriter('mapeo.mp4', fourcc, 20.0, (2*shape_dibujo[1],shape_dibujo[0]))
    #Video volley
    cap = cv2.VideoCapture('imagenes_videos/video_volley2.mp4')

    
    #Tracker
    ct = CentroidTracker(maxDisappeared=60)

    #Trackbar para la altura sobre la malla
    cv2.namedWindow('Personas')
    cv2.createTrackbar('H sobre malla [cm]','Personas',100,200,pass_function)
    cv2.namedWindow('Camera')

    cv2.setMouseCallback('Camera', select)
    calculate_detections = True
    detections_aux = None
    while(True):
        #time1 = time.time()
        ret, image = cap.read()

        if ret==False:
            print("Video terminado")
            break
        #Resize por hardcodeo de puntos
        image = cv2.resize(image,(inputw,inputh))#1920,1080  

        #a veces falla por el video mal grabado uwu
        try:   
            transformation_matrix = getCourtTransformMatrix(image, img_dibujo)
        except:
           continue

        #same
        if(transformation_matrix is None):
            continue

        altura_sobre_malla = cv2.getTrackbarPos('H sobre malla [cm]','Personas')

        #detecciones
        if calculate_detections:            
            detections = model(image)   
            detections_aux = detections
            
        else:
            detections= detections_aux     
        calculate_detections = not calculate_detections

        global Persons_pos,Person_des

        if detections[0] is not None:            
        
            rects = detections[0].cpu().detach().numpy()[:,:4]
            objects = ct.update(rects)
            
            for obj_id ,(x1, y1, x2, y2) in objects.items():         

                x1 = int(x1.item())
                y1 = int(y1.item())
                x2 = int(x2.item())
                y2 = int(y2.item())
                
                color = (148.0, 81.0, 165.0)
                color_selection = (82.0, 162.0, 140.0)  
                Persons_pos.append([str(obj_id),x1,y1,x2,y2])

                punto_cancha = np.array([x1, y2])
                punto_proyectado = transform_point(punto_cancha, transformation_matrix)

                if len(Person_des)>0 and str(int(obj_id))==Person_des[0]:
                    color=color_selection
                    orientacion, elevacion, velocidad = calculo_orientacion_elevacion_velocidad(punto_proyectado, altura_sobre_malla = altura_sobre_malla)

                    angulo_servo_1, angulo_servo_2 = angulos_motores(orientacion, elevacion)

                    string_para_arduino = "{:.2f}#{:.2f}#{:.2f}".format(angulo_servo_1,angulo_servo_2,velocidad)
                    string_2 = "orientacion: {} elevacion: {}".format(orientacion,elevacion)

                    print(string_2)
                    if arduino_on:
                    	if (iterador_comunicacion%n_frames_comunicacion==0):
                        	arduino.write(string_para_arduino.encode())

                    	iterador_comunicacion+=1

                # Dibujar en imagen
                cv2.rectangle(image, (x1, y1), (x2, y2), color, 2)
               
                text =  str(obj_id)
                cv2.rectangle(image,(x1-2,y1-25) , (x1 + 10,y1) , color,-1)
                cv2.putText(image,text,(x1,y1-5), FONT, 0.5,(255,255,255),1,cv2.LINE_AA)                

                #Dibujar puntos a dibujo
                cv2.circle(img_dibujo,(int(punto_proyectado[0]),int(punto_proyectado[1])), 10, color, -1)
        
        cv2.circle(img_dibujo,posicion_omni, 10, (0,0,255), -1)
        out_frame = img_dibujo
        cv2.imshow('Personas', out_frame)#out_frame
        cv2.imshow('Camera', cv2.resize(image,(outputw,outputh)))
        
       # print(time.time()-time1)
        # cv2.namedWindow( "court", cv2.WINDOW_NORMAL  )
        # cv2.imshow('court', img_dibujo)

        #Para no sobreescribir dibujo
        img_dibujo = img_dibujo_copy.copy()

        if save_video:
            out.write(out_frame)

        if cv2.waitKey(1) & 0xFF == ord('q'):
            break

    #arduino.close()
    cap.release()
    if save_video:
        out.release()
if __name__ == '__main__':
    main()

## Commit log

2019-05-09 Agrega codigos motor y disenhos
    [Omni Wrist.cfg, Omni Wrist.stl, baseomni.stl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]
2019-05-10 cambios implementacion
    *Se agrega funcion que calcule el delay.
    *Se agrega factor dos para el calculo de pulsos.
2019-05-15 modifica control posicion y control velocidad para 1 motor
2019-05-15 agrega lista de materiales y hardware electrico
    [lista hardware.xlsx]
2019-05-27 Agrega funcion en matlab para simular las parabolas
2019-05-27 Corrección ángulo
    *Corrección de calculo de ángulo de salida
2019-05-31 Gráficos fancy
    *Graficos fancy para gif
2019-06-11 Agrega ejemplo de transformacion de imagen
2019-06-17 agrega calibracion de motores y calculo de angulos y velocidad en vision
2019-06-17 Programa para calibracion en arduino
2019-06-17 Calculo de parabolas en Python
2019-06-17 Update parabolas.m
    *Cambio de parámetros para comparación con Python
2019-06-18 Update calibracion_motor.ino
    *Comentarios
    *Fin de carrera 180
2019-06-26 Create recepcionWiFi.ino
    *Método para la separación de strings (mensaje recibido)
2019-07-09 agrega documentacion del lanzamiento de parabolas
2019-07-09 Agrega documentacion omniwrist
    [Omni Wrist.cfg, Omni Wrist.stl, baseomni.stl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]
2019-07-09 Ordena código de calibración
    *Agregar comentarios-
    *Eliminar variables no utilizadas
2019-07-14 Agrega codigo arduino para comunicar con python y mover el omniwrist
2019-07-14 Documentacion arduino_python
2019-07-15 Actualizacion Person_Volley desde el otro repo
2019-07-17 Coords. por wifi para motores
2019-07-17 modifica disenhos y agrega orificios
    [brazo corto.stl, brazo largo servo.stl, brazo largo.stl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]
2019-07-19 corrige calculo de lanzamiento
    [calculosLanzamiento.py]
